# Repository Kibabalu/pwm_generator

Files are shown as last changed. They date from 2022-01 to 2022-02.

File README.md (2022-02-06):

# PWM power output generator

PWM power output generator for utilization in training arangements.

Generates a 0 to 100% duty cycle to the load at the output. The dyty cycle can be controlled by an potentiometer. Operating voltage 12VDC. Max. current 3A. In addition it features Inverse supply voltage protection and over-voltage protection. The board fits into a Hammond 1593K enclosure.

Most of PWM generator designs are based on 555 ICs. But I haven't found a circuit that covers up the full range from 0 to 100% duty cycle. Thus I used a more basic design: A combination of a Schmitt trigger and a Integrator, both implemented with two opamps (TLV2372), is feeding a comparator (TLV2372). The duty cycle of the resulting PWM signal is determind by the switching voltage comming from a potentiometer. A complementary driver, made by a NPN (BC817) and a PNP (BC807) transistor, drives a MOSFET (TSM900n06CW) for the load.

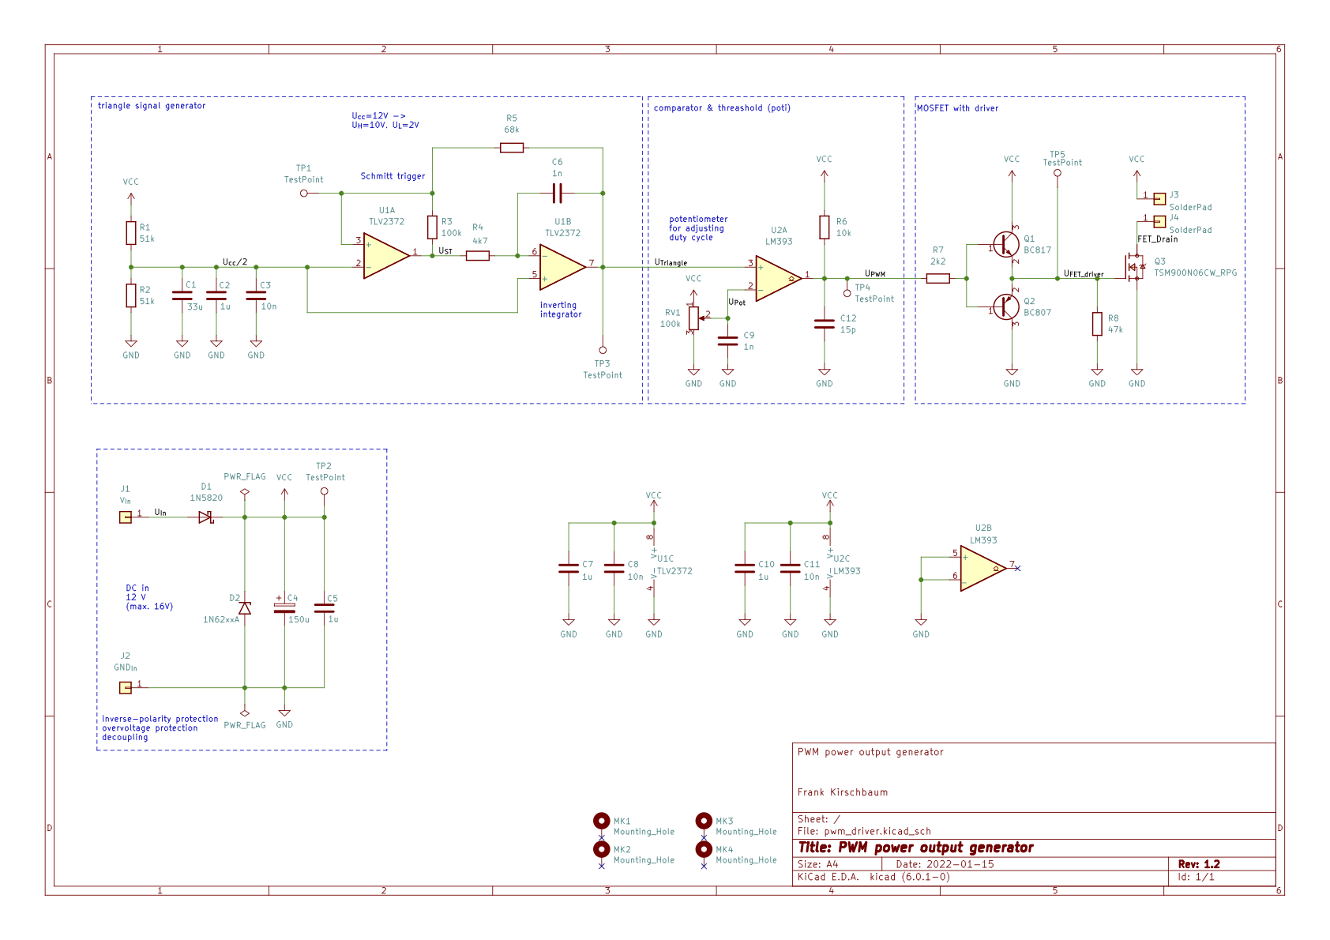
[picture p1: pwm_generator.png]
schematic


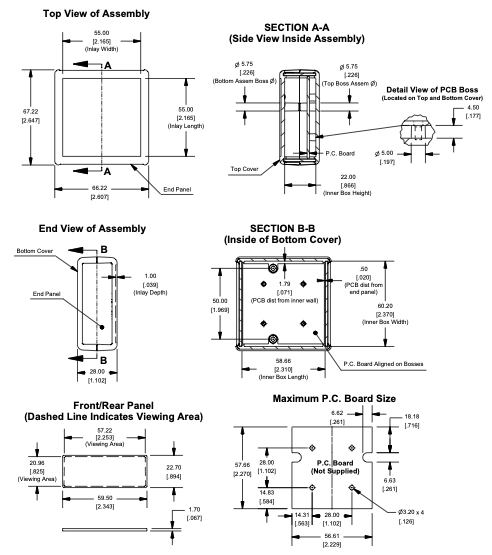
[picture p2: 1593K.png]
Enclosure


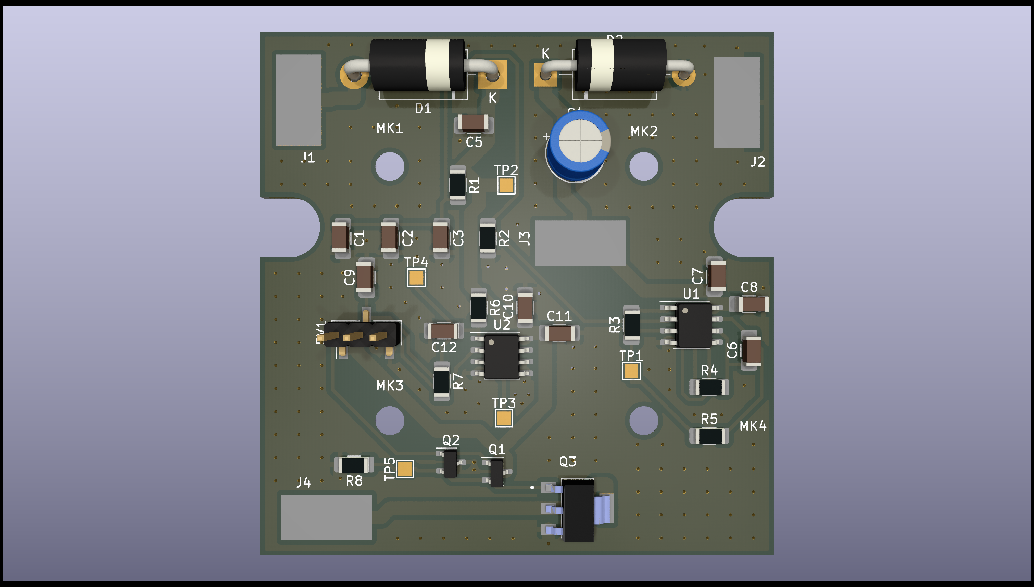
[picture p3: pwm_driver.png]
PCB


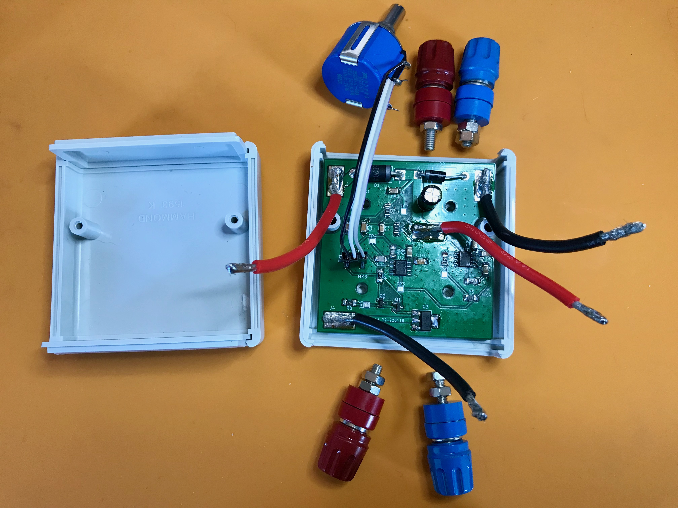
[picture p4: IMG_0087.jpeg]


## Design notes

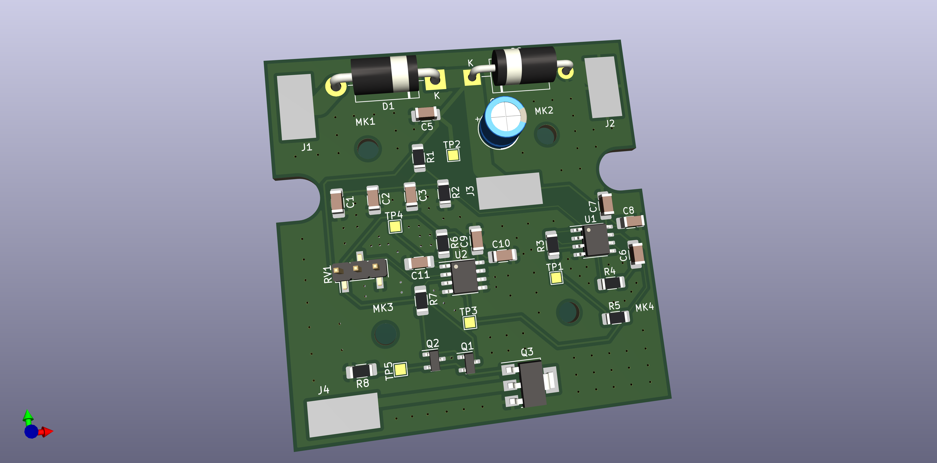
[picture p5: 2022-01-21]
pwm_driver_pcb_3d.png

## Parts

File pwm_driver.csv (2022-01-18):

Source: | /Users/frankkirschbaum/Documents/KiCad/projects/pwm_driver/pwm_driver.kicad_sch
Date: | Sonntag, 16. Januar 2022 um 18:08:40
Tool: | Eeschema (6.0.0-0)
Generator: | /Applications/KiCad/KiCad.app/Contents/SharedSupport/plugins/bom_csv_grouped_by_value_with_fp.py
Component Count: | 50
Ref | Qnty | Value | Cmp name | Footprint | Description | Vendor
C1, | 1 | 10u | C | Capacitor_SMD:C_1206_3216Metric_Pad1.33x1.80mm_HandSolder | Unpolarized capacitor
C2, C5, C7, C10, | 4 | 1u | C | Capacitor_SMD:C_1206_3216Metric_Pad1.33x1.80mm_HandSolder | Unpolarized capacitor
C3, C8, C11, | 3 | 10n | C | Capacitor_SMD:C_1206_3216Metric_Pad1.33x1.80mm_HandSolder | Unpolarized capacitor
C4, | 1 | 150u | C_Polarized | Capacitor_THT:CP_Radial_D6.3mm_P2.50mm | Polarized capacitor
C6, | 1 | 1n | C | Capacitor_SMD:C_1206_3216Metric_Pad1.33x1.80mm_HandSolder | Unpolarized capacitor
C9, | 1 | 15p | C |  | Unpolarized capacitor
D1, | 1 | 1N5820 | 1N5820 | Diode_THT:D_DO-201AD_P15.24mm_Horizontal | 20V 3A Schottky Barrier Rectifier Diode, DO-201AD
D2, | 1 | 1N62xxA | 1N62xxA | Diode_THT:D_DO-201AE_P15.24mm_Horizontal | 1500W unidirectional TRANSZORB® Transient Voltage Suppressor, DO-201AE
D3, | 1 | LED | LED | LED_SMD:LED_1206_3216Metric_Pad1.42x1.75mm_HandSolder | Light emitting diode
J1, J5, | 2 | 105-1102-001 | 105-1102-001 | digikey-footprints:Test_Jack_Horiz | CONN TIP JACK SOLDER RED
J2, J6, | 2 | 105-1103-001 | 105-1103-001 | digikey-footprints:Test_Jack_Horiz | CONN TIP JACK SOLDER BLACK
J3, | 1 | Conn_01x02_Male | Conn_01x02_Male | Connector_PinHeader_2.54mm:PinHeader_1x02_P2.54mm_Vertical_SMD_Pin1Left | Generic connector, single row, 01x02, script generated (kicad-library-utils/schlib/autogen/connector/)
J4, | 1 | Conn_Coaxial | Conn_Coaxial | Connector_Coaxial:BNC_TEConnectivity_1478035_Horizontal | coaxial connector (BNC, SMA, SMB, SMC, Cinch/RCA, LEMO, ...)
MK1, MK2, MK3, MK4, | 4 | Mounting_Hole | Mounting_Hole_PAD-Mechanical | Mounting_Holes:MountingHole_3.2mm_M3_ISO7380
Q1, Q2, | 2 | BC847 | BC847 | Package_TO_SOT_SMD:SOT-23 | 0.1A Ic, 45V Vce, NPN Transistor, SOT-23
Q3, | 1 | BC817 | BC817 | Package_TO_SOT_SMD:SOT-23 | 0.8A Ic, 45V Vce, NPN Transistor, SOT-23
Q4, | 1 | BC807 | BC807 | Package_TO_SOT_SMD:SOT-23 | 0.8A Ic, 45V Vce, PNP Transistor, SOT-23
Q5, | 1 | BUK7880-55A | BUK7880-55A | Package_TO_SOT_SMD:SOT-223-3_TabPin2 | 7A Id, 55V Vds, N-Channel Enhancement Mode MOSFET, SOT-223
R1, R2, R5, | 3 | 100k | R | Resistor_SMD:R_1206_3216Metric_Pad1.30x1.75mm_HandSolder | Resistor
R3, | 1 | 4k7 | R | Resistor_SMD:R_1206_3216Metric_Pad1.42x1.75mm_HandSolder | Resistor
R4, | 1 | 100 | R | Resistor_SMD:R_1206_3216Metric_Pad1.42x1.75mm_HandSolder | Resistor
R6, | 1 | 4k7 | R | Resistor_SMD:R_1206_3216Metric_Pad1.30x1.75mm_HandSolder | Resistor
R7, | 1 | 47k | R | Resistor_SMD:R_1206_3216Metric_Pad1.30x1.75mm_HandSolder | Resistor
R8, | 1 | 10k | R | Resistor_SMD:R_1206_3216Metric_Pad1.30x1.75mm_HandSolder | Resistor
R9, | 1 | 2k2 | R | Resistor_SMD:R_1206_3216Metric_Pad1.30x1.75mm_HandSolder | Resistor
R10, R11, | 2 | 10R | R | Resistor_SMD:R_1206_3216Metric_Pad1.30x1.75mm_HandSolder | Resistor
RV1, | 1 | 100k | R_Potentiometer | Potentiometer_THT:Potentiometer_Piher_PC-16_Single_Horizontal | Potentiometer
TP1, TP2, TP3, TP4, TP5, TP6, TP7, | 7 | TestPoint | TestPoint | TestPoint:TestPoint_Pad_1.5x1.5mm | test point
U1, | 1 | TLV2372 | TLV2372 | Package_SO:SOIC-8-1EP_3.9x4.9mm_P1.27mm_EP2.41x3.81mm_ThermalVias | Dual Rail-to-Rail Input/Output Operational Amplifier, DIP-8/SOIC-8/VSSOP-8
U2, | 1 | LM393 | LM393 | Package_SO:SOIC-8-1EP_3.9x4.9mm_P1.27mm_EP2.41x3.81mm_ThermalVias | Low-Power, Low-Offset Voltage, Dual Comparators, DIP-8/SOIC-8/TO-99-8

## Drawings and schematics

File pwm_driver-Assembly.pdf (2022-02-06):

A

A

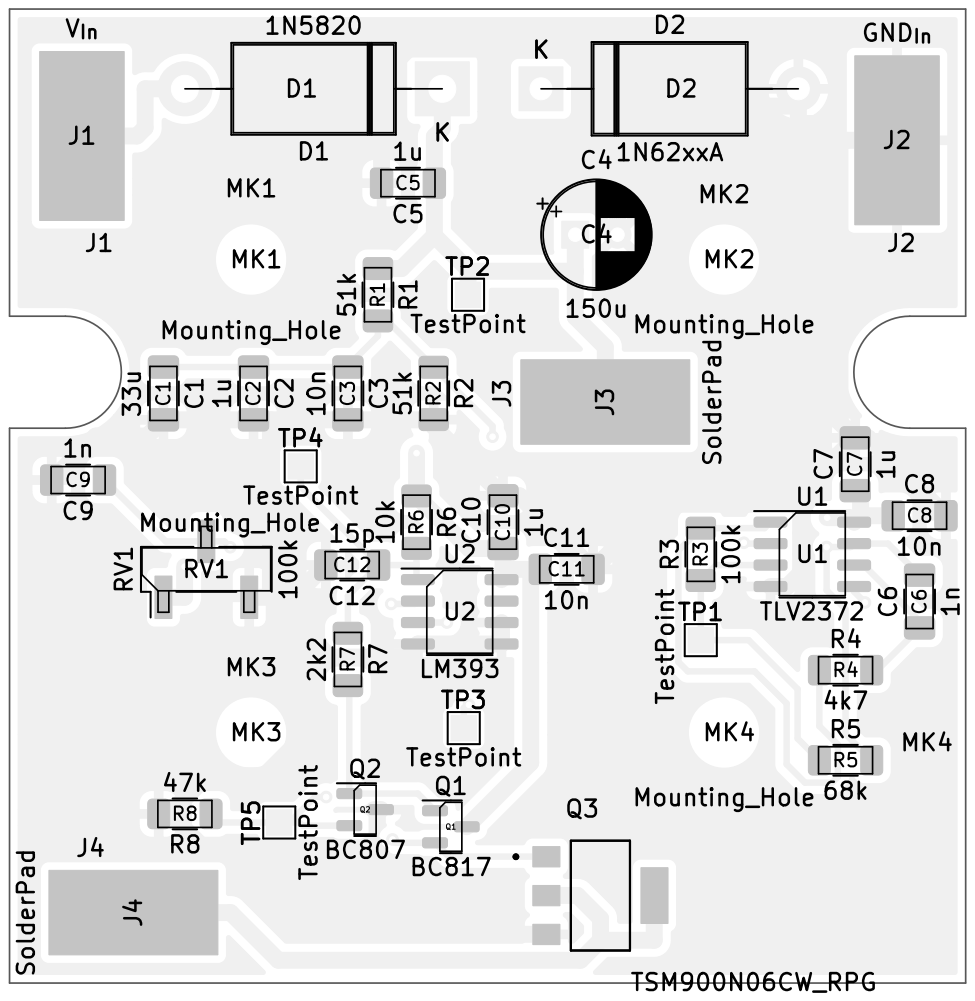
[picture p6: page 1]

Ct Cherrytree Frank Kirschbaum
Sheet: Assembly
File: pwm_driver.kicad_pcb
Id: 1/1 Title: PWM power output generator

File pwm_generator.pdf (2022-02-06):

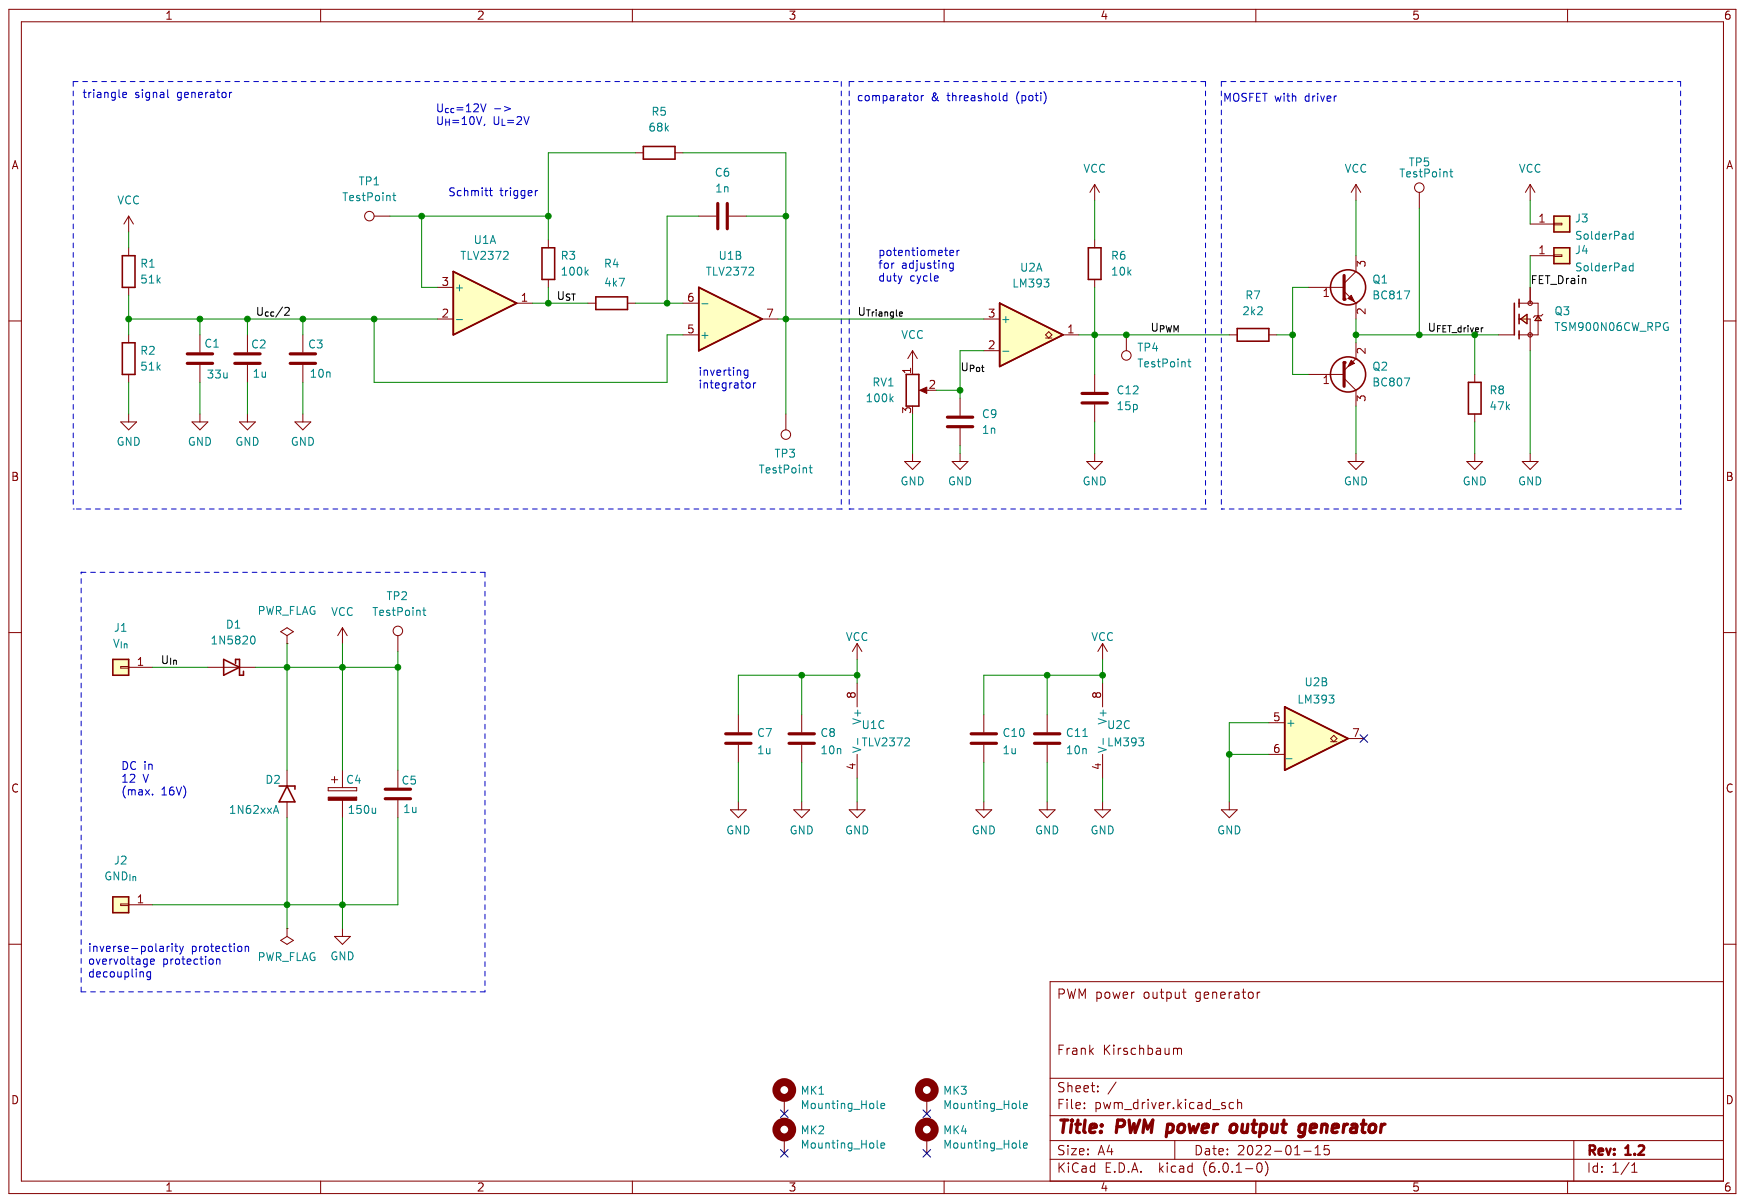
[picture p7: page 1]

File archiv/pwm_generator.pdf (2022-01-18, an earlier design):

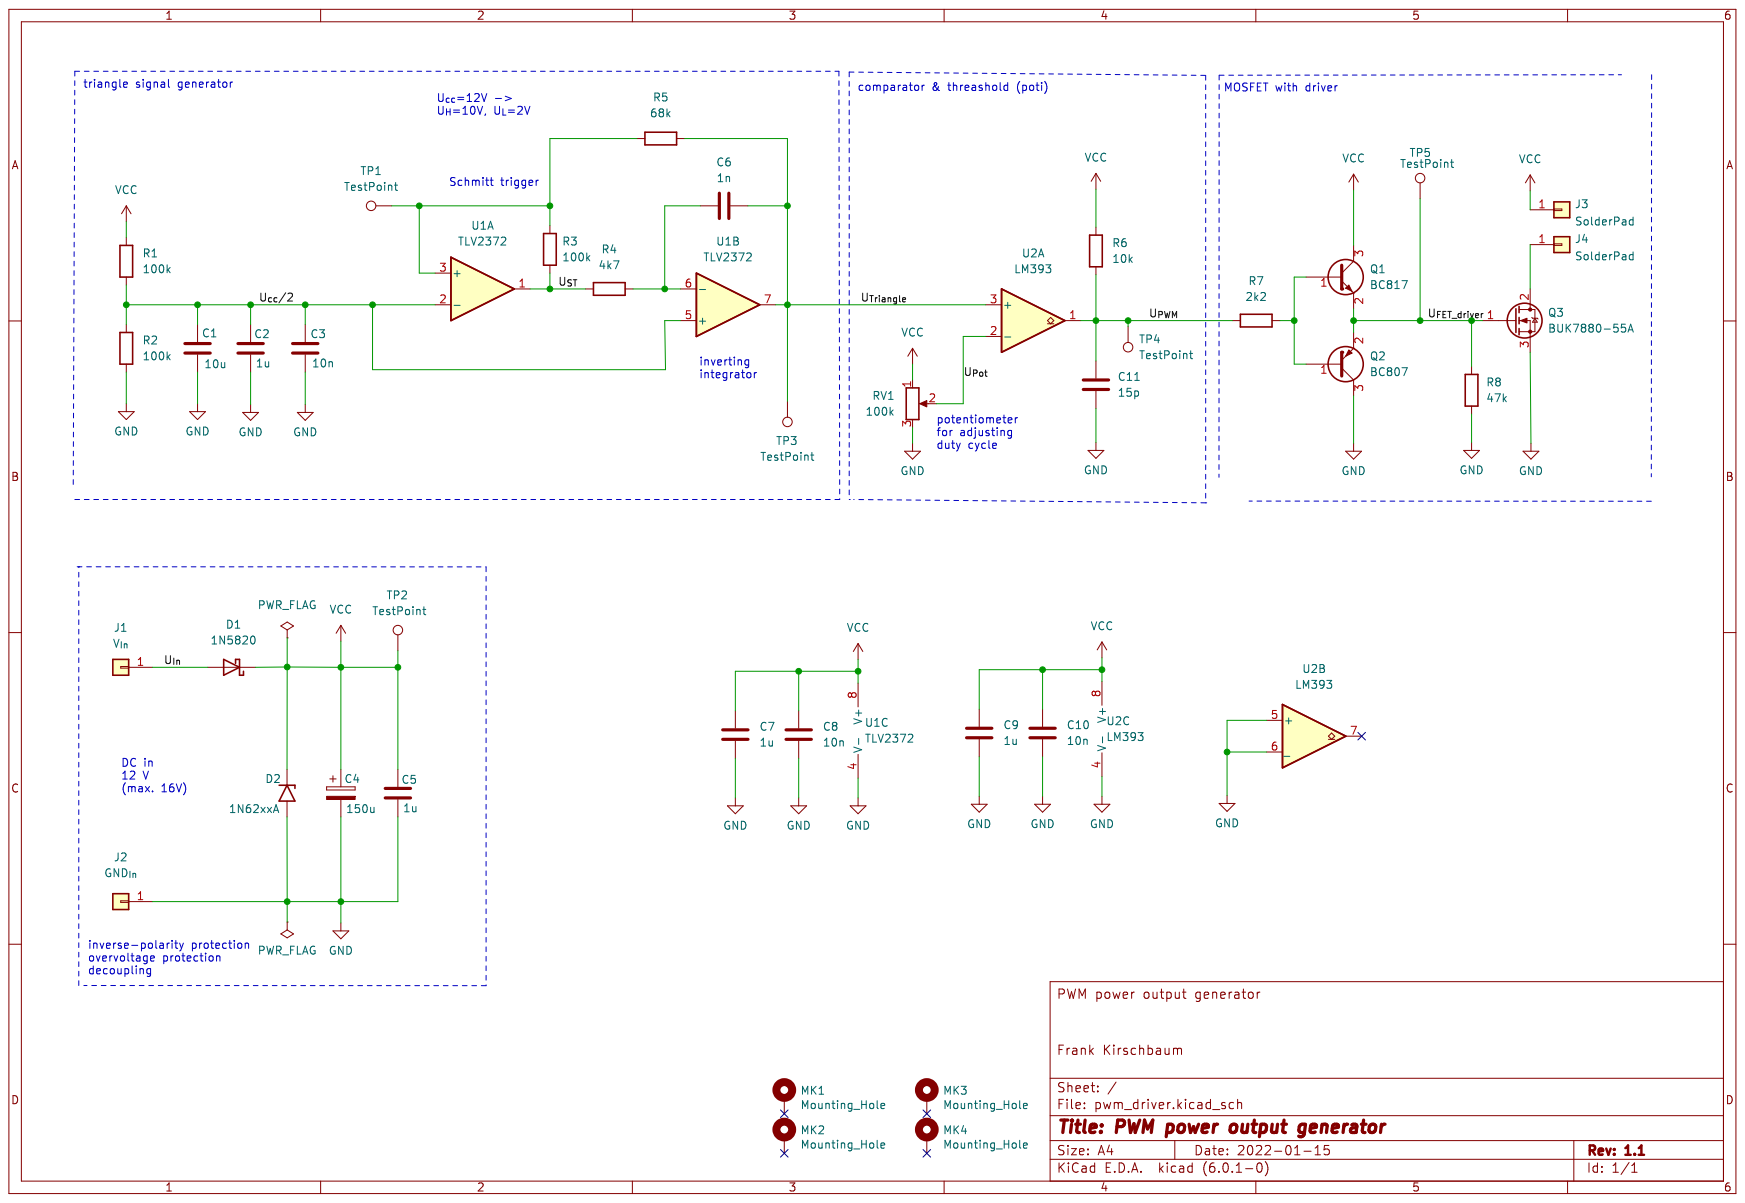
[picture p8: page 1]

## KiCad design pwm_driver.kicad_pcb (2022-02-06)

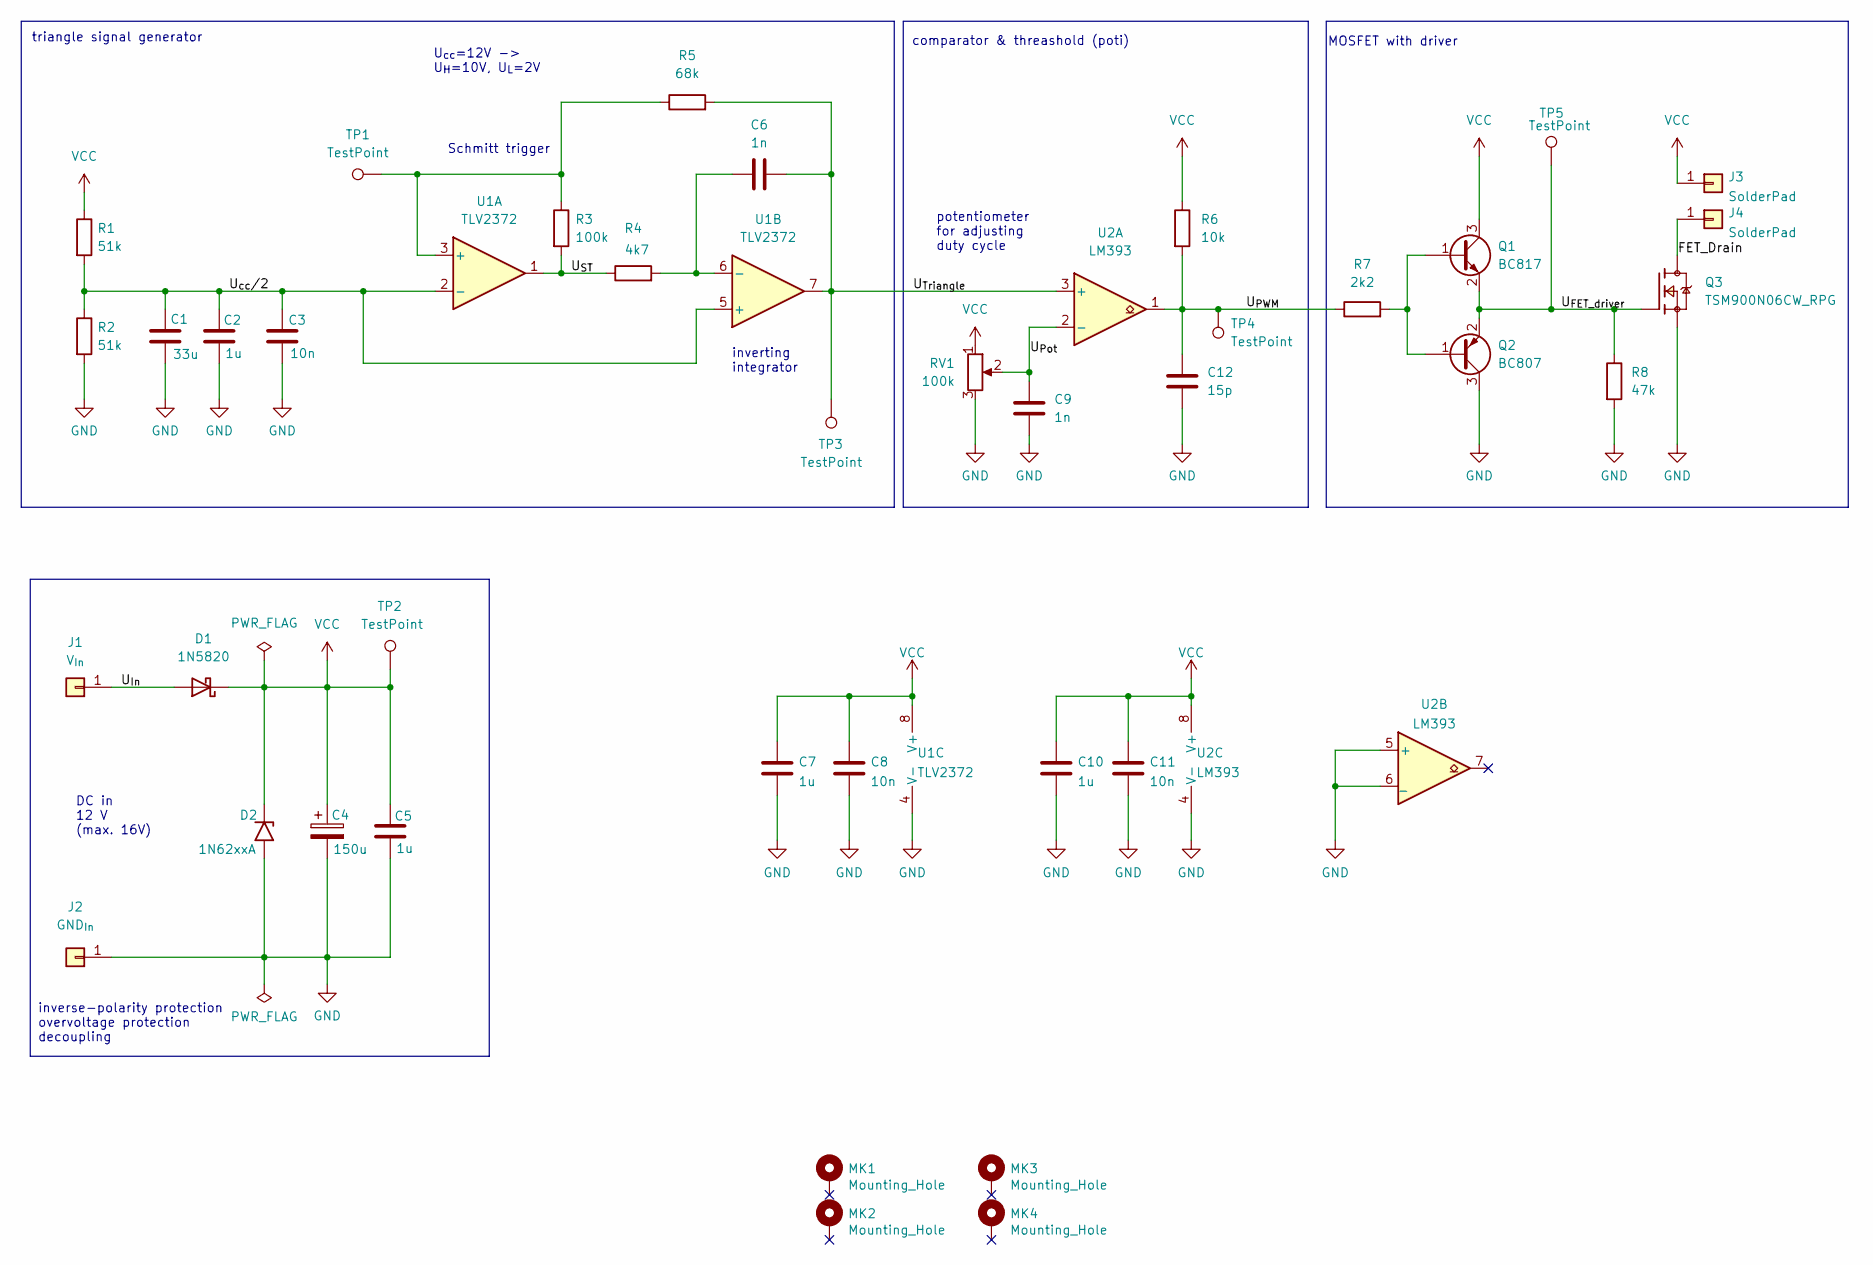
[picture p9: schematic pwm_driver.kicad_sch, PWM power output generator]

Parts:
C1: 33u; C_1206_3216Metric_Pad1.33x1.80mm_HandSolder
C2, C5, C7, C10: 1u; C_1206_3216Metric_Pad1.33x1.80mm_HandSolder
C3, C8, C11: 10n; C_1206_3216Metric_Pad1.33x1.80mm_HandSolder
C4: 150u; CP_Radial_D6.3mm_P2.50mm
C6, C9: 1n; C_1206_3216Metric_Pad1.33x1.80mm_HandSolder
C12: 15p; C_1206_3216Metric_Pad1.33x1.80mm_HandSolder
D1: 1N5820; D_DO-201AD_P15.24mm_Horizontal
D2: 1N62xxA; D_DO-201AE_P15.24mm_Horizontal
J1: V_{In}; SolderWirePad_1x01_SMD_5x10mm
J2: GND_{In}; SolderWirePad_1x01_SMD_5x10mm
J3, J4: SolderPad; SolderWirePad_1x01_SMD_5x10mm
MK1: Mounting_Hole; MountingHole_3.2mm_M3
MK2, MK3, MK4: Mounting_Hole; MountingHole_3.2mm_M3_ISO7380
Q1: BC817; SOT-23
Q2: BC807; SOT-23
Q3: TSM900N06CW_RPG; TRANS_TSM900N06CW_RPG; PARTREV D1706
R1, R2: 51k; R_1206_3216Metric_Pad1.30x1.75mm_HandSolder
R3: 100k; R_1206_3216Metric_Pad1.30x1.75mm_HandSolder
R4: 4k7; R_1206_3216Metric_Pad1.30x1.75mm_HandSolder
R5: 68k; R_1206_3216Metric_Pad1.30x1.75mm_HandSolder
R6: 10k; R_1206_3216Metric_Pad1.30x1.75mm_HandSolder
R7: 2k2; R_1206_3216Metric_Pad1.30x1.75mm_HandSolder
R8: 47k; R_1206_3216Metric_Pad1.30x1.75mm_HandSolder
RV1: 100k; PinHeader_1x03_P2.54mm_Vertical_SMD_Pin1Left
TP1, TP2, TP3, TP4, TP5: TestPoint; TestPoint_Pad_1.5x1.5mm
U1: TLV2372; SOIC-8_3.9x4.9mm_P1.27mm
U2: LM393; SOIC-8_3.9x4.9mm_P1.27mm

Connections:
/FET_Drain: J4.1, Q3.2, Q3.4
/U_{FET_driver}: Q1.2 (E), Q2.2 (E), Q3.1, R8.1, TP5.1
/U_{In}: D1.2 (A), J1.1
/U_{PWM}: C12.1, R6.2, R7.1, TP4.1, U2.1
/U_{Pot}: C9.1, RV1.2, U2.2 (-)
/U_{ST}: R3.2, R4.1, U1.1
/U_{Triangle}: C6.2, R5.2, TP3.1, U1.7, U2.3 (+)
/U_{cc}/2: C1.1, C2.1, C3.1, R1.2, R2.1, U1.2 (-), U1.5 (+)
GND: C1.2, C2.2, C3.2, C4.2, C5.2, C7.2, C8.2, C9.2, C10.2, C11.2, C12.2, D2.2 (A2), J2.1, Q2.3 (C), Q3.3, R2.2, R8.2, RV1.3, U1.4 (V-), U2.4 (V-), U2.5 (+), U2.6 (_)
unnamed: C6.1, R4.2, U1.6 (-)
unnamed: Q1.1 (B), Q2.1 (B), R7.2
unnamed: R3.1, R5.1, TP1.1, U1.3 (+)
VCC: C4.1, C5.1, C7.1, C8.1, C10.1, C11.1, D1.1 (K), D2.1 (A1), J3.1, Q1.3 (C), R1.1, R6.1, RV1.1, TP2.1, U1.8 (V+), U2.8 (V+)

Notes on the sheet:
Schmitt trigger
inverse-polarity protection overvoltage protection decoupling
comparator & threashold (poti)
U_{cc}=12V -> U_{H}=10V, U_{L}=2V
potentiometer for adjusting duty cycle
MOSFET with driver
triangle signal generator
DC in 12 V (max. 16V)
inverting integrator

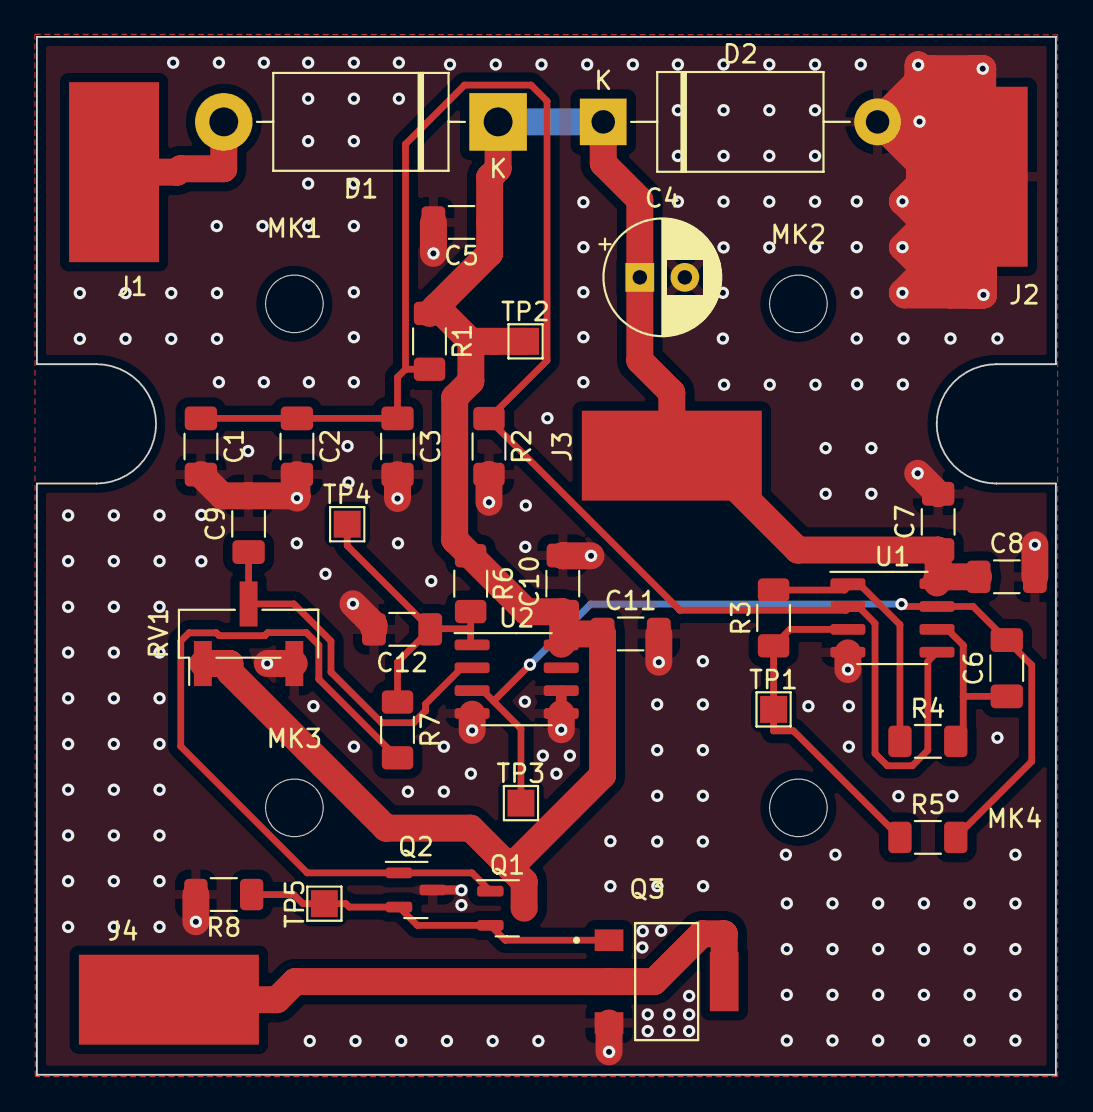
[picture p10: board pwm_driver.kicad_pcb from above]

Board: 2 copper layers, 56.6 x 57.7 mm, 41 parts (0 on the bottom side), 13 nets.

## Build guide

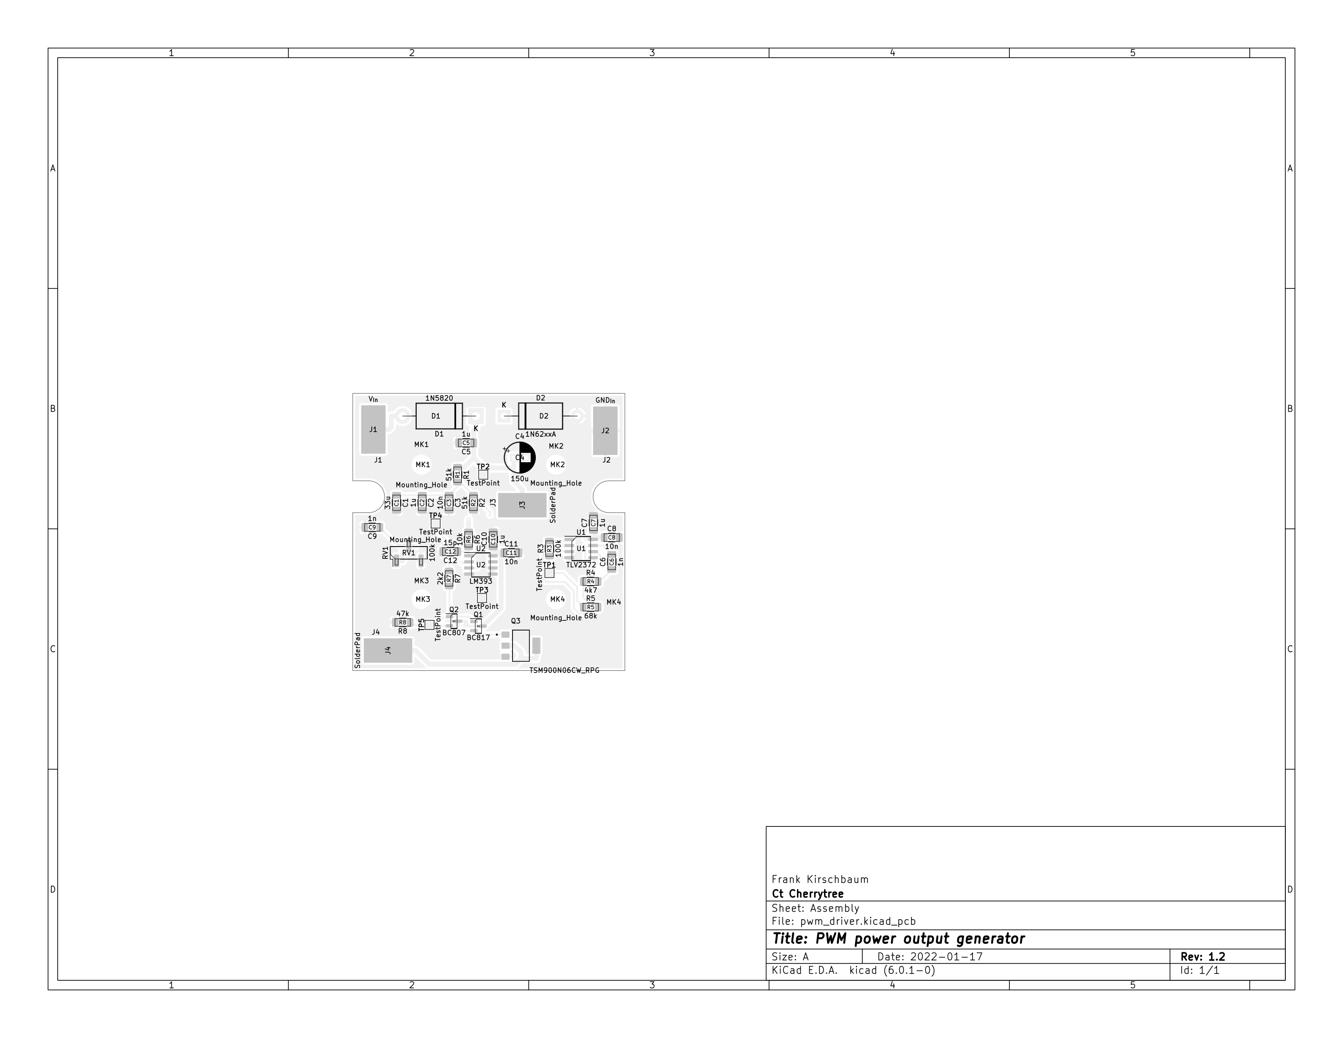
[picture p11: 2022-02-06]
pwm_driver-Assembly.png

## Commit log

2022-01-18 1st commit
    [BOM-pwm_driver.csv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]
2022-01-19 export jlcpcb
    [pwm_driver.dsn]
2022-01-20 minor redesign (decoupling cap)
    [BOM-pwm_driver.csv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]
2022-01-21 pcb board 3d picture added
2022-02-03 subfolder with simulation model added
    [pwm_driver.kicad_pcb, pwm_driver.kicad_sch, sim.kicad_pcb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]
2022-02-03 some cleaning
    [BOM-pwm_driver.csv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]
2022-02-04 simulation model error fix
    [sim.kicad_sch]
2022-02-05 some more simulation stuff
    [sim.kicad_sch]
2022-02-05 added smoothing capacitor for potentiometer output, improved routing
    [pwm_driver.dsn]
2022-02-05 photo added from working device
    [pwm_driver.dsn, pwm_driver.kicad_sch]
2022-02-06 README.md edited
    [pwm_driver.kicad_pcb]
2022-02-06 documentation edited
    [pwm_driver.kicad_sch]
2022-02-06 trace width modified for higher currents
    [pwm_driver.kicad_pcb]
2022-02-06 minor layout modifications
    [pwm_driver.kicad_pcb]
2022-02-06 new §D rendering
    [pwm_driver.kicad_pcb]
2022-02-06 some more GND vias added
    [pwm_driver.kicad_pcb]
